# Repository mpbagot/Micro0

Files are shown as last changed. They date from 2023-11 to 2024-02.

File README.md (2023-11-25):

# Micro 0, a 1010 Makerbeam-based Voron 0 printer

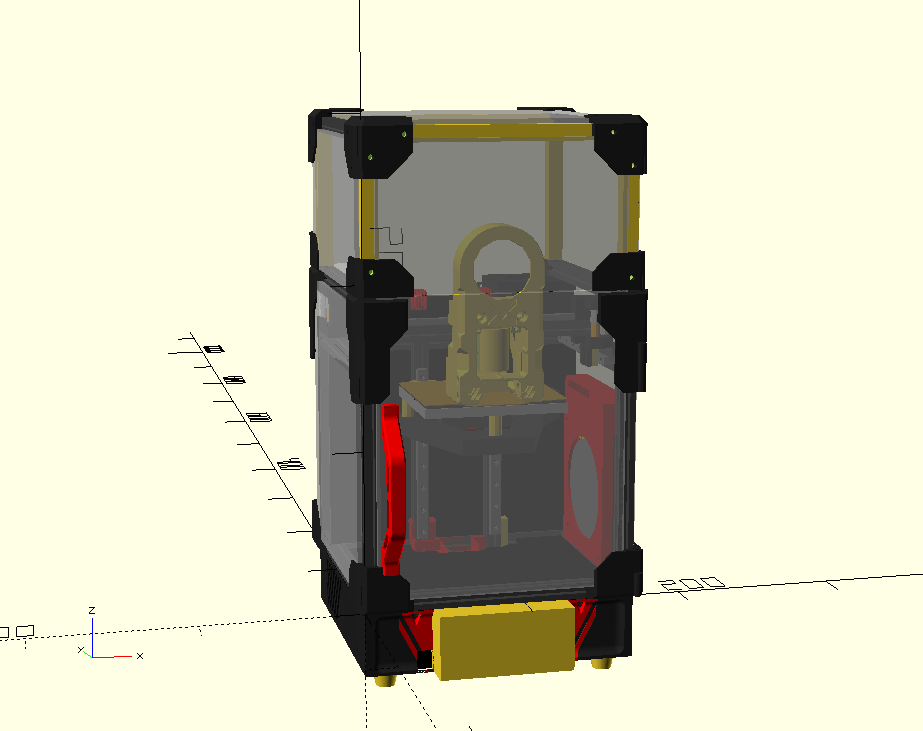
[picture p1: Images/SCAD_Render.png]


This is an attempt at producing the smallest practically-sized Voron 0 style printer that could be made. This makes use of 10x10mm Makerbeam extrusions, in the standard 150mm lengths, alongside the typical NEMA14's of a Voron 0.

The current design makes use of a modified [Mailbox toolhead by chirpy2605](https://github.com/chirpy2605/voron/tree/main/V0/Mailbox), and with the enclosure sealed has a print volume of 90x70x75mm. With the door and tophat removed, the rails should allow for 90x80x80mm of travel. Further work would need to be done on the toolhead to allow for this.

The external footprint of the printer is 179x179x338mm, including panel clips and a 100mm tophat.

## Project status: Beta/WIP

This is a very early work in progress. It is highly recommended to be extremely familiar with the V0 build process before starting. Expect to have to figure things out as you go, and refer to both the CAD and standard V0 manual as appropriate.

That said, any suggestions or improvements are welcome. All issues and pull requests will be looked at.

## Hardware/BOM

This printer requires mostly similar hardware to a standard V0, though many pieces are scaled down. Bolts are on a best-fit basis, and exact counts aren't known. Test what works, generally opting for the same, or slightly shorter than stock.

- The standard F623-RS flanged bearings are replaced by F683zz bearings (3x7x3mm). The standard bearings are too large in diameter and interfere with panels.
- The X and Y rails are replaced by [MGN5 rails](https://www.aliexpress.com/item/1005004714467036.html). The X must be 120mm, whilst the Y should both be 100mm. The Z rails are still MGN7H rails, but should be cut to 115-120mm in length.
- For the MGN5 rails, standard M2 bolts will not allow for the carriage to move. [These M2x6x3 screws](https://www.robotdigg.com/product/1010/Slim-head-set-screws-for-linear-rails) from RobotDigg are confirmed suitable.
- Makerbeams require special M3 nuts that they sell in packs of 25. 3 packs (75 nuts) are sufficient, with some excess. 50 may work in a pinch, but some modifications to the design will be required.
- Makerbeams fit some standard hex M2 nuts. I used excess M2 nuts from a Formbot V0 kit, and found that around 5% of them would fit, whilst most were too large. Unfortunately, I do not know where to source M2 nuts that fit consistently.
- This design uses the standard 150mm extrusions sold by Makerbeam. These are sold in packs of 6. The main body uses 16, with a 100mm tophat requiring an additional 6. However, I've included printed parts to replace the front and back extrusion of the tophat, meaning the complete design can be made with 18 extrusions (3 packs of 6).

## Build Advice/Other Things to Consider

### Print orientation

Most pieces are not oriented correctly at all. For most pieces, following the orientation of the original V0 is fine. Please note that for the XY joint top pieces, supports are needed, since I have only cut standard cylinders for the bolt holes.

Perhaps most importantly, the panel clips need to be printed with supports on 45 degree angles. Printing the clips as per the V0 orientation will result in the clip-in part snapping easily. For strength, the layers need to stack along the length of the clip part. This unfortunately necessitates support material. Any better design suggestions that don't rely on excessive use of nuts would be greatly appreciated.

### Makerbeams

The 10x10 Makerbeams have a similar groove profile to 1515 extrusions. Importantly, clip-in pieces for 1515 extrusions should just fit, albeit a little tightly.

The depth of the channel is around 2.5mm from the outer face of the extrusion. M3 nuts are flush with the outer face, whilst M2 nuts would be recessed 1mm. 5mm bolts are best for the Z-axis, and most bolts should be 1-2mm shorter than the equivalent in a Voron 0.

### Electronics

The BOM power supply of the Voron 0, the LRS-150 is larger than the available space in this design. My build made use of an AC bed, and thus I used a [90W Mean Well power supply (MPM-90-24ST)](https://au.mouser.com/ProductDetail/MEAN-WELL/MPM-90-24ST). DC beds will obviously require a larger power supply, but there may exist other options than the LRS-150.

Although a full-sized Raspberry Pi should fit, a Pi Zero W or Zero 2W is highly recommended for ensuring more free space and air flow.

### Heated Bed

Most heat mats are too large for use with this bed. [Custom silicone heater pads](https://www.aliexpress.com/item/1005005170757163.html) are around, but if you want a heated bed, it will not be as simple as buying a Voron preset heater.

According to the 0.4W/cm^2 rule, a 30W mat would be good, but I personally use a 15W mat (as that is all the seller offered), that is sufficient albeit a little slow to heat. If you can find a 30W heater, I would recommend it.

### Bed

The bed is custom sized. At present, there exists no supplier for them, so there are some DXFs included under "DXFs/bed" for cutting the bed out of a piece of 6mm or 1/4" aluminium using a CNC mill. For my build, screw holes were countersunk to 4mm depth with a flat end mill.

Also, [Energetic](https://energetic3d.aliexpress.com/store/4542004) on Aliexpress sell custom PEI plates, and I have found their plates to be good.

### Auxiliary Cooling

A very simple auxiliary cooler based on a 7515 cooling fan is included. It's not a very good design, but functions well enough for my purposes. It can be included, removed, or modified as needed.

## Credits/Attribution

The following models included in this repository are taken from other places.
 - "Cowl_NoProbe.stl" and "Dragon_Mount.stl" by chirpy2605 on [Github](https://github.com/chirpy2605/voron/tree/main/V0/Mailbox). Used under GPL3.0.
 - "PrintedVoronFoot.stl" by stoneburner on [Printables.](https://www.printables.com/model/633391-printed-voron-v02-foot) Used under public domain license terms.
 - The following models are taken from the [Voron 0 STLs](https://github.com/VoronDesign/Voron-0/tree/Voron0.2r1/STLs):
  - "[a]_Tensioner_Knob_x2.stl"
  - "[a]_Cable_Tie_x1.stl"
  - "[a]_B_Drive_Tensioner_x1.stl"
  - "[a]_A_Drive_Tensioner_x1.stl"
  - "[a]_9mm_Spacer_x6.stl"
  - "X_Carriage_x1.stl" (renamed to "carriage.stl")
 - "[a]_fan_grill_A_x2.stl" (renamed to "[a]_fan_grill.stl") by hartk from [Micron Github](https://github.com/PrintersForAnts/Micron/blob/main/STLs/Skirts/SideFanSkirts/%5Ba%5D_fan_grill_A_x2.stl). Used under GPL3.0.

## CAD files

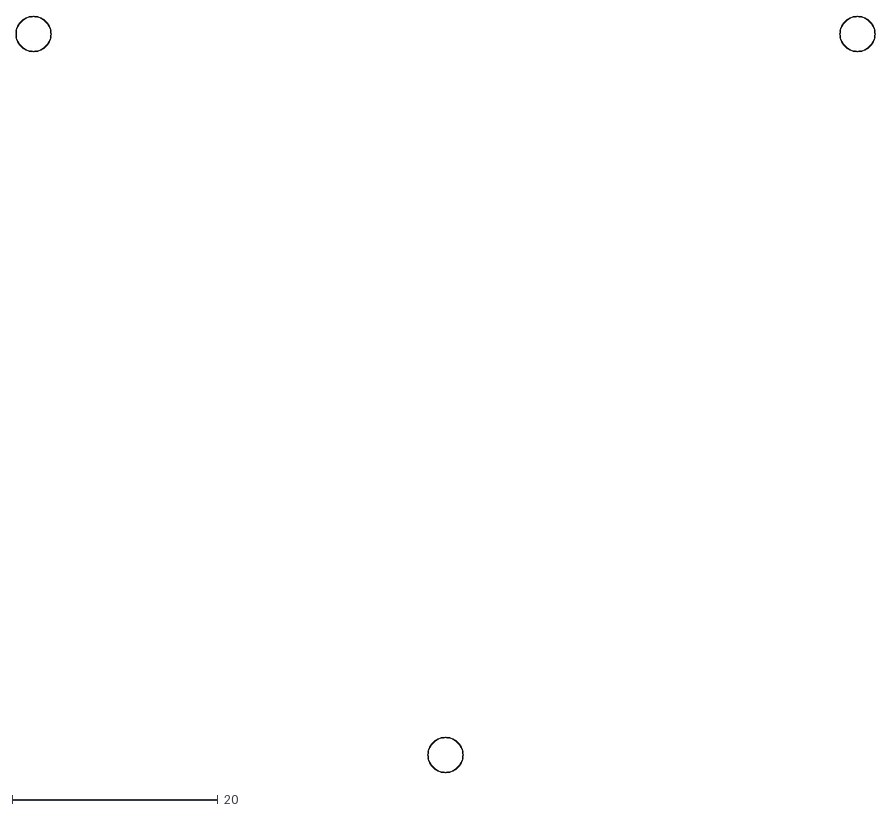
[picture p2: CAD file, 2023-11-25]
DXFs/bed/plunge_holes.dxf
83.4 x 73.4

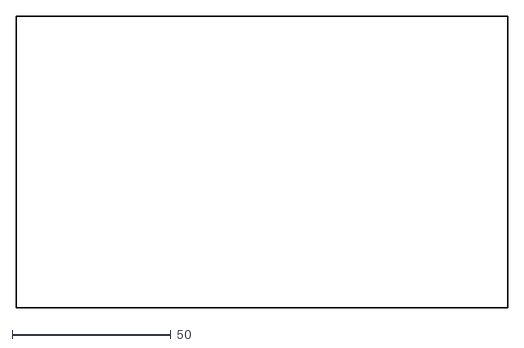
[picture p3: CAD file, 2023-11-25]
DXFs/tophat_side_panel.dxf
155.0 x 92.0

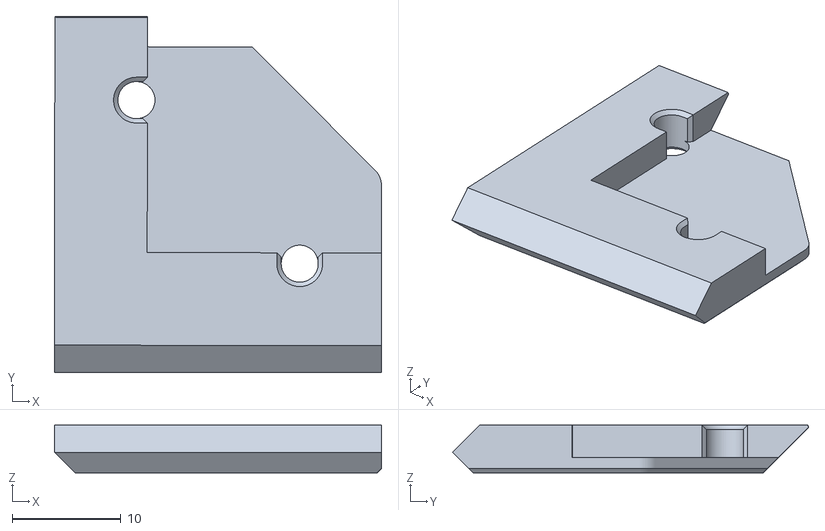
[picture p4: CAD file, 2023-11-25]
Panel_Mounting/Left_Bottom_Rear_Panel_Clip_x1.stl
30.0 x 32.7 x 4.40

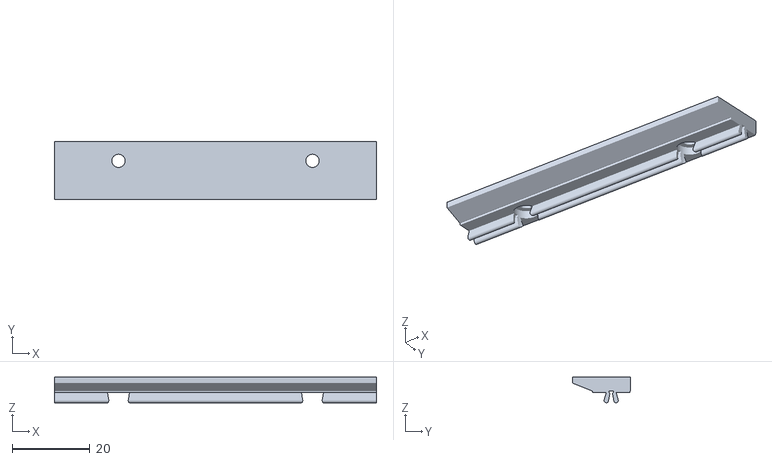
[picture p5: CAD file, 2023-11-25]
STLs/Aux Cooler/aux_cooling_base_clip.stl
83.0 x 15.0 x 6.60

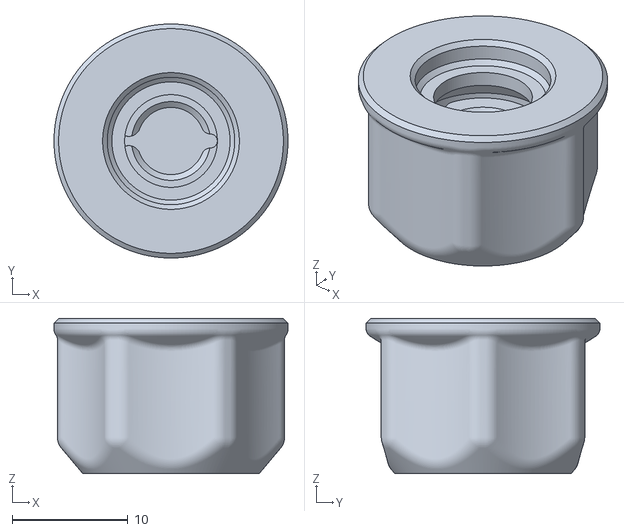
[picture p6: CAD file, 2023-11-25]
STLs/Electronics/Display_Knob_x1.stl
20.2 x 20.2 x 13.4

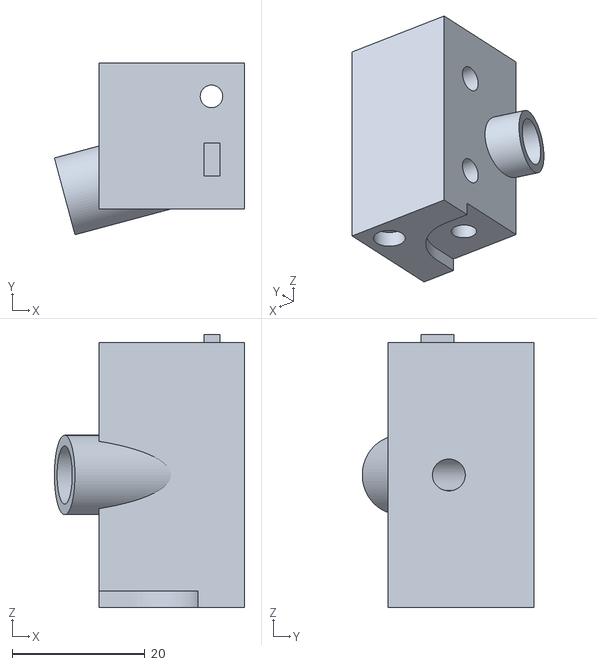
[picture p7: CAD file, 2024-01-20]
STLs/Feet/foot_rear_right.stl
28.7 x 25.9 x 41.2

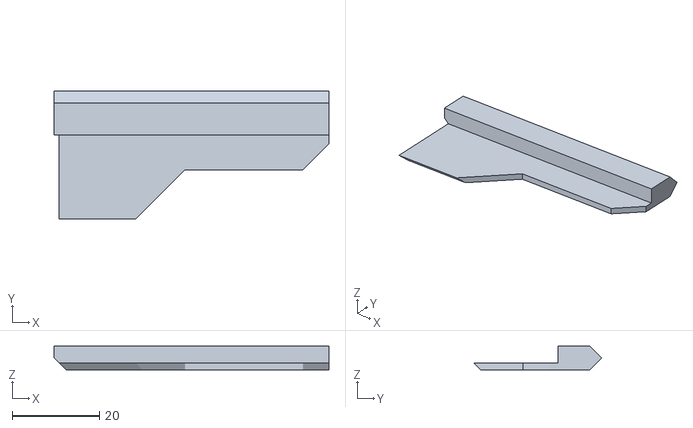
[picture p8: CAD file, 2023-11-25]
STLs/Panels/1mm Foam Tape/top_left_door.stl
63.0 x 29.2 x 5.40

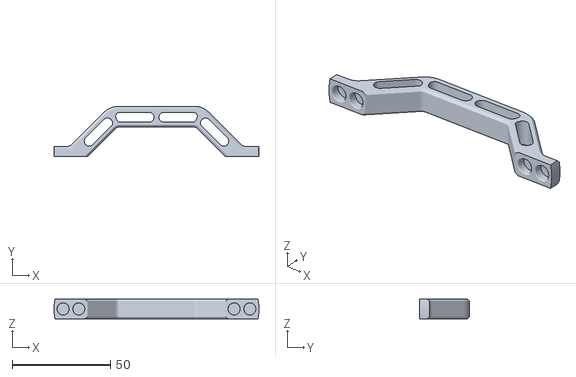
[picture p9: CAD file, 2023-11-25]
STLs/Panels/Door/Door_Handle_x1.STL
104.3 x 25.5 x 10.0

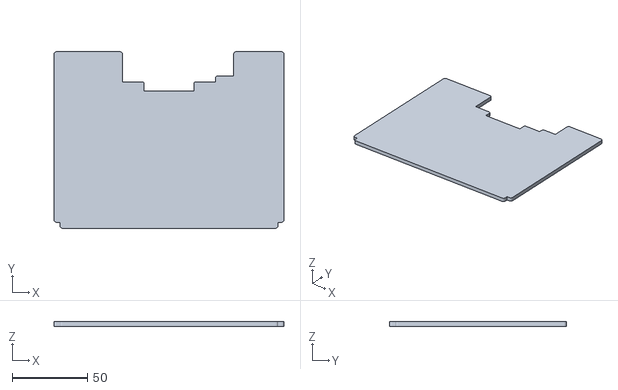
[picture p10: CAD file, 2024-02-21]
STLs/Panels/Printed Panels/deck_panel.stl
153.0 x 117.4 x 3.00

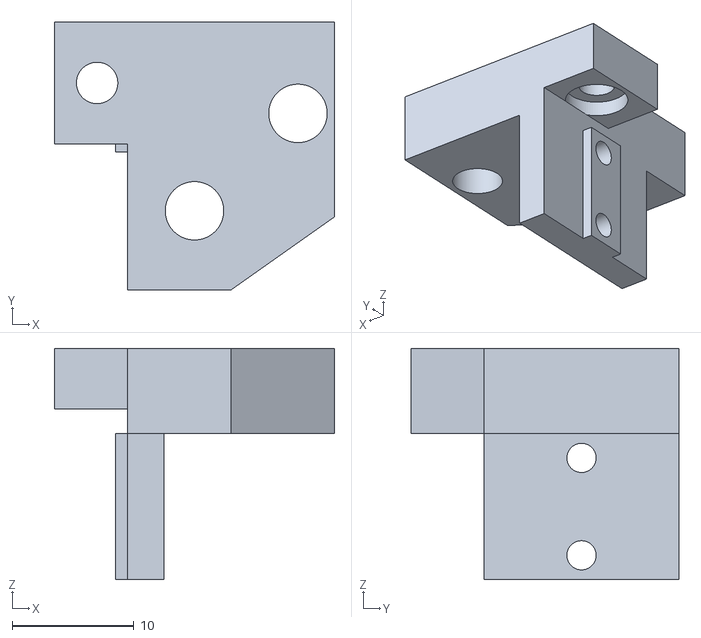
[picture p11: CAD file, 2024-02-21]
STLs/r_xy_joint_bottom.stl
23.0 x 22.0 x 19.0

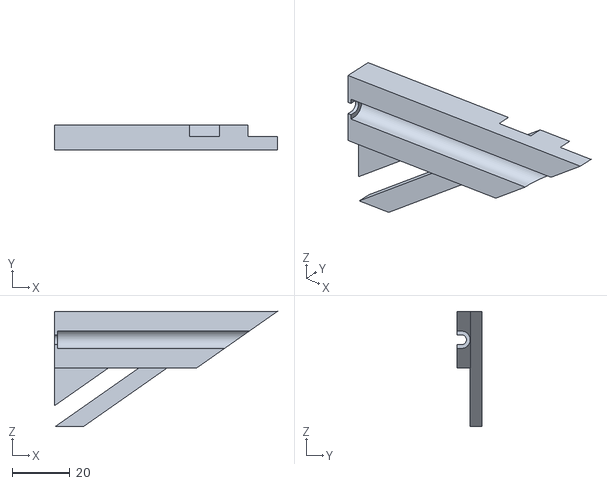
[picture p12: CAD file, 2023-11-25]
STLs/Skirts/Angled_Skirts/rear_skirt_insert.stl
77.0 x 8.51 x 39.8

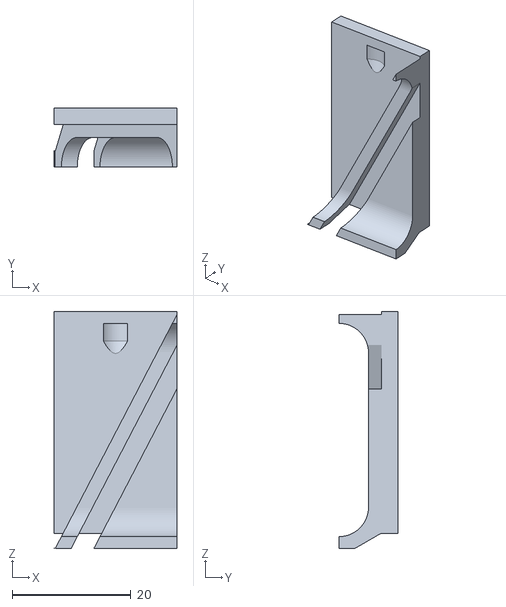
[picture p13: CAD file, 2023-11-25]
STLs/Skirts/front_skirt_right_body.stl
20.8 x 10.0 x 40.0

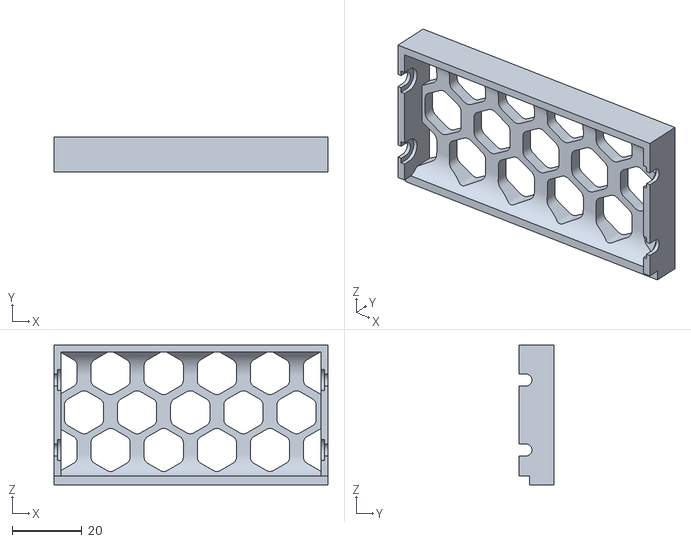
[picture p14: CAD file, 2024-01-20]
STLs/Skirts/Honeycomb_Skirts/rear_skirt.stl
78.4 x 10.0 x 40.0

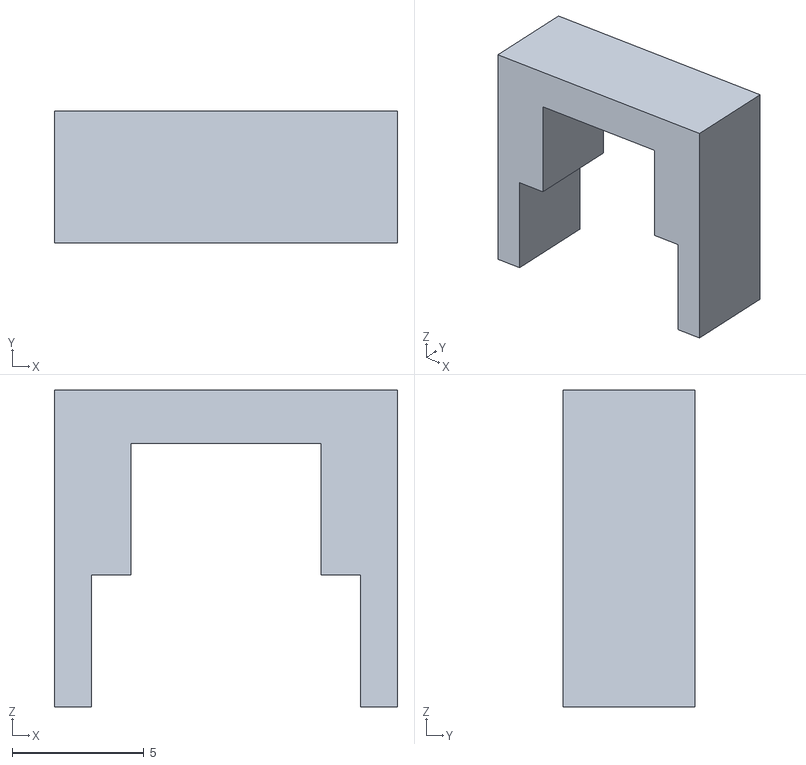
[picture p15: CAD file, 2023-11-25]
STLs/Tools and Jigs/mgn7_rail_aligner.stl
13.0 x 5.00 x 12.0

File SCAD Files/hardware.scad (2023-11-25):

//$fa = 2;
$fs = 0.5;

include <params.scad>;

module bearing_stack() {
    // Bearing stack total height is 9mm
    color("silver") union() {
    // Bottom shim
    cylinder(h=0.5, r=3);
    // Bottom bearing
    translate([0, 0, 0.5]) cylinder(h=0.8, r=4.05);
    translate([0, 0, 1.3]) cylinder(h=2.2, r=3.5);
    
    // Middle shims
    for (i=[0:3]) {
        translate([0, 0, 3.5+0.5*i]) cylinder(h=0.5, r=3);
    }
    
    // Top bearing
    translate([0, 0, 5.5]) cylinder(h=2.2, r=3.5);
    translate([0, 0, 7.7]) cylinder(h=0.8, r=4.05);
    // Top shim
    translate([0, 0, 8.5]) cylinder(h=0.5, r=3);
    }
}

module spacer() {
    color("orange") cylinder(r=3, h=9);
}

// Generate a rail of given length, with the carriage at percentage 'pos' along it's length, where pos is between 0 and 1
module mgn5_rail(length, pos) {
    // rail
    // TODO
    color("gray") difference() {
        translate([0, -2.5, 0]) cube([length, 5, 3.6]);
        
        // Screw holes
        for (i = [5:15:length]) {
            translate([i, 0, 3.6-0.8]) cylinder(r=1.8, h=4);
            translate([i, 0, -2]) cylinder(r=1.2, h=10);
        }
    }
    
    // carriage
    difference() {
        translate([length*pos - MGN5_CARR_LEN/2, -6, 1.5]) cube([MGN5_CARR_LEN, 12, 4.5]);
        
        // Screw holes in carriage
        translate([length*pos, 4, 4.5]) cylinder(r=1, h=1.6);
        translate([length*pos, -4, 4.5]) cylinder(r=1, h=1.6);
    }
}

module mgn7_rail(length, pos) {
    // rail
    // TODO
    color("Gray") difference() {
        translate([0, -3.5, 0]) cube([length, 7, 4.8]);
        
        // Screw holes
        for (i = [5:15:length]) {
            translate([i, 0, 3.6-0.8]) cylinder(r=1.8, h=4);
            translate([i, 0, -2]) cylinder(r=1.2, h=10);
        }
    }
    
    // carriage
    difference() {
        translate([length*pos - MGN7_CARR_LEN/2, -8.5, 1.5]) cube([MGN7_CARR_LEN, 17, 6.5]);
        
        // Screw holes in carriage
        translate([length*pos+6.5, 6, 5.5]) cylinder(r=1, h=2.6);
        translate([length*pos+6.5, -6, 5.5]) cylinder(r=1, h=2.6);
        translate([length*pos-6.5, 6, 5.5]) cylinder(r=1, h=2.6);
        translate([length*pos-6.5, -6, 5.5]) cylinder(r=1, h=2.6);
    }
    
}

module st3h_rail(length, pos) {
    // rail
    // TODO
    color("Gray") difference() {
        translate([0, -1.5, 0]) cube([length, 3, 2.6]);
        
        // Screw holes
        for (i = [5:10:length]) {
            translate([i, 0, 3.6-0.8]) cylinder(r=1.8, h=4);
            translate([i, 0, -2]) cylinder(r=.8, h=10);
        }
    }
    
    // carriage
    difference() {
        translate([length*pos - ST3H_CARR_LEN/2, -4, 1]) cube([ST3H_CARR_LEN, 8, 3]);
        
        // Screw holes in carriage
        translate([length*pos+2.75, 0, 2.7]) cylinder(r=1, h=2.6);
        translate([length*pos-2.75, 0, 2.7]) cylinder(r=1, h=2.6);
    }
    
}

module rail_stop() {
    
    // 3mm tall, 10mm wide, 2.2mm hole, and about 6mm deep
    module shape() {
        difference() {
            cube([6, 10, 3]);
            
            translate([0, -sqrt(2), 0]) rotate([0, 0, 45]) cube([2, 2, 5]);
            translate([0, 10-sqrt(2), 0]) rotate([0, 0, 45]) cube([2, 2, 5]);
        }
    }
    difference() {
        hull() {
            shape();
        
            translate([.6, 1, 1.8]) scale([0.8, 0.8, 0.8]) shape();
        }
        
        // Screw hole
        translate([3, 5, -0.01]) cylinder(r=1.1, h=50);
    }
}

module ssr_mount() {
    // 20mm apart, 28.5mm apart
    difference() {
        union() {
            // Base
            hull() {       
                translate([17-14.25, 12.5-10, 0]) cylinder(r=3, h=3);
                translate([17-14.25, 12.5+10, 0]) cylinder(r=3, h=3);
                translate([17+14.25, 12.5-10, 0]) cylinder(r=3, h=3);
                translate([17+14.25, 12.5+10, 0]) cylinder(r=3, h=3);
            }
            
            // Legs
            translate([17-14.25, 12.5-10, 3]) cylinder(r=3, h=5);
            translate([17-14.25, 12.5+10, 3]) cylinder(r=3, h=5);
            translate([17+14.25, 12.5-10, 3]) cylinder(r=3, h=5);
            translate([17+14.25, 12.5+10, 3]) cylinder(r=3, h=5);
        }
        
        // Screw holes
        translate([17-14.25, 12.5-10, -1]) cylinder(r=.8, h=50);
            translate([17-14.25, 12.5+10, -1]) cylinder(r=.8, h=50);
            translate([17+14.25, 12.5-10, -1]) cylinder(r=.8, h=50);
            translate([17+14.25, 12.5+10, -1]) cylinder(r=.8, h=50);
    }
}

translate([-10, 0, 0]) bearing_stack();

mgn5_rail(150, 0.5);

translate([0, 20, 0]) mgn7_rail(150, 0.5);

translate([0, 40, 0]) st3h_rail(150, 0.5);

translate([-10, 15, 0]) rail_stop();

translate([-35, 40, 0]) ssr_mount();

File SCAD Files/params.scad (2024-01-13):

EXTRUSION_LEN = 150;
MOTOR_SIZE = 1.4*25.4;

MGN5_CARR_LEN = 16;
MGN7_CARR_LEN = 30.8;
ST3H_CARR_LEN = 15.5;

BED_X = 90;
BED_Y = 80;

MAIN = "#202020";
ACCENT = "red";

TOPHAT_HEIGHT = 100;

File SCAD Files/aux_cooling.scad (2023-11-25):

include <params.scad>;
use <clip.scad>;

$fn = 40;

module aux_cooler() {
    translate([0, -2, 37.5]) rotate([90, 0, 0]) fan();
    
    // Back plate
    color(MAIN) translate([-1.5, -5, 40]) back_plate();
    
    // Funnel/front plate
    color(ACCENT) translate([-43.5, -15, -6]) funnel();
    
    // Clip-in base
    color(MAIN) base_clip();
}

module funnel() {
    difference() {
        union() {
            hull() {
                translate([.5, -2, 86]) cube([83, 17, 20]);
                translate([5.5, -2, 106]) cube([73, 14, 5]);
            }
            
            // Front plate piece
            translate([.5, -2, 0]) cube([83, 7, 86]);
        }
        
        // Fan hole
        translate([42.5, 14, 6]) translate([0, -2, 37.5]) rotate([90, 0, 0])  cylinder(d=67, h=14.1);
        
        // Funnel hole
        translate([43.5, 14, 6]) translate([-37, -15, 37.5]) cube([74, 6.1, 60.5]);
        translate([43, 14, 6]) translate([0, -1.4, 37.5]) rotate([90, 0, 0])  cylinder(d=75, h=13.6);
        
        hull() {
            translate([43.5, 14, 6]) translate([-32, -14, 97.5]) cube([64, 5.1, 5.5]);
            translate([43.5, 19, 1]) translate([-37, -14, 83.5]) cube([74, 8, 19.5]);
        }
        hull() {
            translate([43.5, 14, 6]) translate([-37, -17, 97.5]) cube([74, 15.1, .5]);
            translate([43.5, 14, 6]) translate([-32, -17, 97.5]) cube([64, 5.1, 5.5]);
        }
        
        // Rear plate screw holes
        translate([36+84/2, -5.01, -41.01+46]) rotate([-90, 0, 0]) cylinder(h=15, r=1.7);
        translate([-31+84/2, -5.01, -36.01+46]) rotate([-90, 0, 0]) cylinder(h=15, r=1.7);
        translate([-36+84/2, -5.01, 35.01+46]) rotate([-90, 0, 0]) cylinder(h=15, r=1.7);
    }
}

module back_plate() {
    difference() {
        translate([0, 0, -3]) cube([83, 10, 86], center=true);
        
        // Base mounting insert holes
        translate([0, 0, -46.01]) union() {
            translate([25, 0, 0]) cylinder(h=5, r=2.4);
            translate([-25, 0, 0]) cylinder(h=5, r=2.4);
        }
        
        // Front plate insert holes
        translate([36, -5.01, -41.01]) rotate([-90, 0, 0]) cylinder(h=5, r=2.4);
        translate([-31, -5.01, -36.01]) rotate([-90, 0, 0]) cylinder(h=5, r=2.4);
        translate([-36, -5.01, 35.01]) rotate([-90, 0, 0]) cylinder(h=5, r=2.4);
        
        // Wire hole
        translate([-39, -5.01, -46]) cube([3, 6, 48]);
        
        // Fan body
        translate([1.5, 2.99, -2.5]) rotate([90, 0, 0]) linear_extrude(8) minkowski() {
            circle(r=1);
            _fan_base();
        }
        
        translate([-7.5, -5.01, 30.01]) cube([46.5, 8, 10]);
        
        // Screw holes
        translate([1.5, 3.98, -2.5]) union() {
            translate([-(40)/sqrt(2), -1, (40)/sqrt(2)]) rotate([-90, 0, 0]) cylinder(h=2.03, r1=1.5, r2=3);
            translate([-(40)/sqrt(2), -10, (40)/sqrt(2)]) rotate([-90, 0, 0]) cylinder(h=12.03, r=1.5);
            
            translate([(40)/sqrt(2), -1, -(40)/sqrt(2)]) rotate([-90, 0, 0]) cylinder(h=2.03, r1=1.5, r2=3);
            translate([(40)/sqrt(2), -10, -(40)/sqrt(2)]) rotate([-90, 0, 0]) cylinder(h=12.03, r=1.5);
        }
    }
}

module _fan_base() {
    union() {
        circle(d=75);
        translate([-(46-75/2), 0]) square([46, 78-75/2]);
        difference() {
            hull() {
                translate([(40)/sqrt(2), -(40)/sqrt(2)]) circle(r=4);
                translate([-(40)/sqrt(2), (40)/sqrt(2)]) circle(r=4);
            }
            
            translate([(40)/sqrt(2), -(40)/sqrt(2)]) circle(r=2);
            translate([-(40)/sqrt(2), (40)/sqrt(2)]) circle(r=2);
        }
    }
}

module fan() {
    linear_extrude(8) _fan_base();
    
    color("grey") cylinder(d=63, h=14.1);
}

module base_clip() {
    difference() {
        union() {
            translate([-1.5, -5, -10]) rotate([90, 0, 90]) clip(83);
            hull() {
                translate([-83/2-1.5, -15, -7.5]) cube([83, 15, 1.5]);
                translate([-83/2-1.5, -10, -9.5]) cube([83, 10, 2]);
            }
        }
        
        // Screw holes
        translate([-26.5, -5, -20]) cylinder(r=1.7, h=50);
        translate([-26.5, -5, -20]) cylinder(r=3.1, h=12);
        
        translate([23.5, -5, -20]) cylinder(r=1.7, h=50);
        translate([23.5, -5, -20]) cylinder(r=3.1, h=12);
    }
}

$fn=120;
funnel();

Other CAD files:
STLs/Tophat/Printed Option/front_printed_ushape.stl
STLs/Tophat/top_corner_right_clip.stl
DXFs/bed/bed_cutout.dxf
DXFs/side_panel.dxf
SCAD Files/bed.scad
DXFs/back_panel_bottom.dxf
DXFs/back_panel_top.dxf
DXFs/base_panel.dxf
DXFs/bed/countersink_holes.dxf
DXFs/deck_panel.dxf
DXFs/door_panel.dxf
DXFs/motor_panel.dxf
DXFs/pei_plate.dxf
DXFs/rear_chamber_panel.dxf
DXFs/tophat_top_panel.dxf
Panel_Mounting/Door_Latch_x2.STL
Panel_Mounting/Front_Bottom_Left_Clip_x1.stl
Panel_Mounting/Front_Bottom_Right_Hinge_x1.stl
Panel_Mounting/Front_Top_Left_Clip_x1.stl
Panel_Mounting/Front_Top_Right_Hinge_x1.stl
Panel_Mounting/Left_Bottom_Front_Panel_Clip_x1.stl
Panel_Mounting/Left_Top_Front_Panel_Clip_x1.stl
Panel_Mounting/Left_Top_Rear_Panel_Clip_x1.stl
Panel_Mounting/Middle_Clip_x9.stl
Panel_Mounting/Rear_Bottom_Left_Clip_x1.stl
Panel_Mounting/Rear_Bottom_Right_Clip_x1.stl
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

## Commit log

2024-01-13 Move TOPHAT_HEIGHT parameter to params.scad
    [panels.scad, params.scad, tophat.scad]
2024-01-20 Rename various accent colour parts
    [[a]_anti_backlash_nut_holder.stl, [a]_rail_stop.stl, [a]_z_endstop.stl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]
2024-01-20 Adjust foot bowden angle and move stls to subdirectory
    [foot_rear_left.stl, foot_rear_right.stl, skirts_feet.scad]
2024-01-20 Add Honeycomb skirt option for sides and rear
    [honeycomb_skirts.scad, main_assembly.scad, rear_skirt.stl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]
2024-02-21 Fix bolt hole sizes
    [gantry.scad, l_xy_joint_bottom.stl, l_xy_joint_top.stl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]
2024-02-21 Add deck and chamber panel STLs
    [deck_panel.stl, rear_chamber_panel.stl]
